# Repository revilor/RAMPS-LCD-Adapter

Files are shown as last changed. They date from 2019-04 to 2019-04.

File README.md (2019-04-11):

# RAMPS-LCD-Adapter

This is an adapter to free pins 16 and 17 on the RAMPS AUX-4 connector usually used for LCDs to be used for the MMU2 serial connection. The LCD I use is the Anet 12864 LCD Smart Display Controller. Other LCDs might work but I can't guarantee for that.

## Marlin 2.0 settings for Anet LCD

To use the Anet LCD with this adapter you have to set the following configuration options in Marlin.

### Configuration.h

```
#define REPRAP_DISCOUNT_FULL_GRAPHIC_SMART_CONTROLLER
```

### pins_RAMPS.h

At the end of the file add

```
// custom pins ANET LCD 12864

#undef LCD_PINS_RS
#undef LCD_PINS_ENABLE
#undef LCD_PINS_D4
#undef LCD_PINS_D5
#undef LCD_PINS_D6
#undef LCD_PINS_D7
#undef BEEPER_PIN

#define LCD_PINS_RS     25
#define LCD_PINS_ENABLE 27
#define LCD_PINS_D4     29
#define LCD_PINS_D5     -1
#define LCD_PINS_D6     -1
#define LCD_PINS_D7     -1
#define BEEPER_PIN        37

#define STD_ENCODER_PULSES_PER_STEP 4
#define STD_ENCODER_STEPS_PER_MENU_ITEM 1

//#define ST7920_DELAY_1 DELAY_1_NOP
//#define ST7920_DELAY_2 DELAY_2_NOP
//#define ST7920_DELAY_3 DELAY_3_NOP

#define ST7920_DELAY_1 DELAY_NS(0)
#define ST7920_DELAY_2 DELAY_NS(63)
#define ST7920_DELAY_3 DELAY_NS(125)
```

## MMU2 connector

The MMU2 connector has the following pins from top to bottom (colors correspond to the original Prusa MMU2 serial cable):

 * +5V (Blue)
 * TX (White)
 * RX (Green)
 * NC
 * Hardware Reset (Brown)

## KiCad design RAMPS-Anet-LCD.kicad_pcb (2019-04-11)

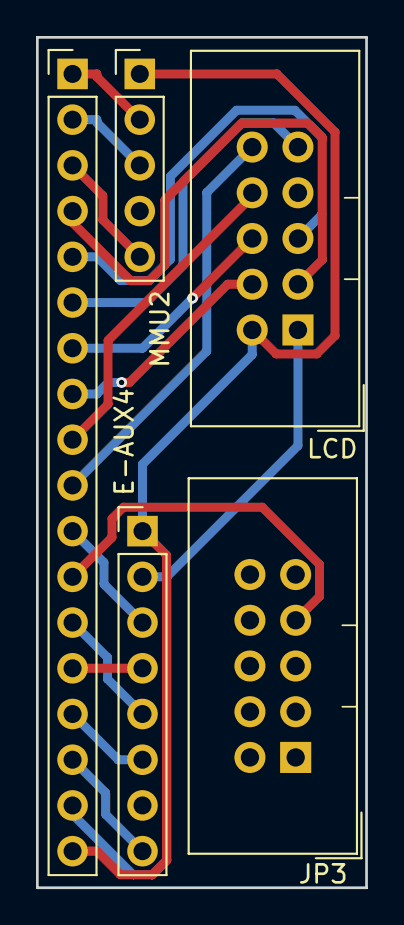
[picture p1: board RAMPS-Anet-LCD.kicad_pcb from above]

Board: 2 copper layers, 18.3 x 47.2 mm, 5 parts (0 on the bottom side), 18 nets.

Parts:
J1: E-AUX4; PinHeader_1x08_P2.54mm_Vertical
J2: LCD; IDC-Header_2x05_P2.54mm_Vertical
J3: JP3; IDC-Header_2x05_P2.54mm_Vertical
J4: MMU2; Pin_Header_Straight_1x05_Pitch2.54mm
J5: AUX-4; Pin_Header_Straight_1x18_Pitch2.54mm

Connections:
+5V: J1.1, J2.2, J4.1, J5.18
/Brown: J4.5, J5.3
/D16: J4.2, J5.1
/D17: J4.3, J5.2
/D25: J2.3, J5.4
/D27: J2.5, J5.5
/D29: J2.9, J5.6
/D31: J2.6, J5.7
/D32: J1.8, J5.16
/D33: J2.4, J5.8
/D35: J2.8, J5.9
/D37: J2.10, J5.10
/D39: J1.3, J5.11
/D41: J3.7, J5.12
/D43: J1.5, J5.13
/D45: J1.4, J5.14
/D47: J1.6, J5.15
GND: J1.2, J2.1, J5.17
